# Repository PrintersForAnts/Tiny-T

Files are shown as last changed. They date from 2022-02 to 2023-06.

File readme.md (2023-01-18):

# Tiny-T (revision 2.0)



Tiny-T is a Voron Trident with build volume 150mm^3.

<p align="center">
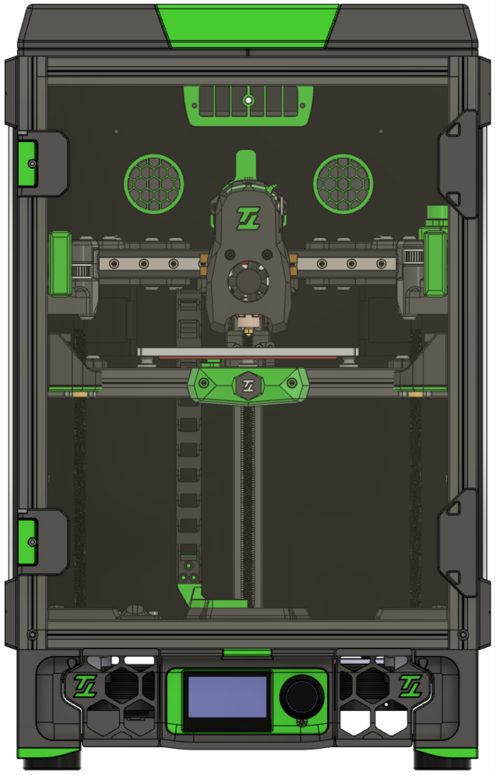
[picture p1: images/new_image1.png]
  
</p>

Source: https://github.com/VoronDesign/Voron-Trident

License: [License](./LICENSE.txt)

Changes: Tiny-T "branding" and scale modelling down.

### Changes from revision 1.0 to revision 2.0

- With the addition of the tophat, the vertical extrusions are now back to 400mm, according to Trident specifications
- Side, Front and Rear panels have reduced their height by also 25mm
- Single front door
- New door hinges and handles
- New rear panel with mounting holes for the air filter
- New bed design that support M3 screws to hold the build plate aligned

Important: if ordering panels from vendors, make sure they are using the latest DXF files

## Frame Specs

If ordering from Misumi, these are the specs:

```
Misumi HFSB5-2020-400-LCP-RCP-AV260		4 (corner extrusion)
Misumi HFSB5-2020-270-TPW 			9 (top, bottom, front[top/bottom], rear top extrusions)
Misumi HFSB5-2020-270-AH135-TPW 		1 (rear bottom extrusion)
Misumi HFSB5-2020-230-LTP			1 (rear Z extrusion)
Misumi HFSB5-2020-230				1 (x gantry extrusion)
Misumi HFSB5-2020-140				1 (rear gantry extrusion)
Misumi HFSB5-2020-270-AH135			1 (bed extrusion)
Misumi HFSB5-2020-132-LTP			1 (bed extrusion)
```

## Components

- 2x 1200mm (120cm) GATE belts
- 6x Linear Rail MGN9H 200mm - [Ali Express](https://www.aliexpress.com/item/32773296501.html?spm=a2g0s.9042311.0.0.6ea64c4dDtOd7b)
- 150mmx150mm bed - [Mandala Roseworks](https://www.mandalaroseworks.com/shop/tiny-t)
- 150mm PEI Flex build plate - [Ali Express](https://www.aliexpress.com/item/1005003157344482.html?spm=a2g0s.9042311.0.0.6ea64c4dDtOd7b)
- 120mmx120mm 120w 24v heating pad - [Keenovo](https://keenovo.store/collections/standard-keenovo-silicone-heaters/products/keenovo-square-silicone-heater-3d-printer-build-plate-heatbed-heating-pad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)
- LDO Orbiter Extruder kit - [Fabreeko](https://www.fabreeko.com/products/ldo-orbiter-extruder-1-75mm?_pos=1&_sid=68aa9064c&_ss=r) OR LDO Galileo Clockwork kit - [Fabreeko](https://www.fabreeko.com/products/ldo-galileo-clockwork-kit?_pos=1&_sid=3b0226477&_ss=r)
- 2x LDO NEMA 17 stepper motors - [Printed Solid](https://www.printedsolid.com/products/ldo-nema-17-motor-high-temp-180c-ldo-42sth40-2004mah)
- 3x V0.1 Z Stepper motor with 150mm lead screw - [Fabreeko](https://www.fabreeko.com/products/ldo-42sth25-1004cl200evrn-v0-1-z-motor?_pos=9&_sid=546ac732a&_ss=r)
- 3x GE5C bearings - [Deep Fried Hero](https://deepfriedhero.in/products/ge5c-spherical-bushing-plain-bearing?_pos=2&_psq=ge&_ss=e&_v=1.0), [Ali Express](https://www.aliexpress.com/item/1005001493222143.html?spm=a2g0s.9042311.0.0.6ea64c4dDtOd7b)
- FYSETC V2.1 RGB Mini 12864 - [Amazon](https://www.amazon.com/gp/product/B08R9ZH7S2/ref=ppx_yo_dt_b_search_asin_title?ie=UTF8&psc=1)
- Amplifier Cabinet - [Amazon](https://www.amazon.com/gp/product/B00JJ191Z6/ref=ppx_yo_dt_b_search_asin_title?ie=UTF8&psc=1), [Ali Express](https://www.aliexpress.com/item/1005001469045379.html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)

### Mods used

- [Boop](https://github.com/VoronDesign/VoronUsers/tree/master/printer_mods/Ellis/Single_MGN9H_Carriage) by `Yeri`
- [RSCS](https://github.com/VoronDesign/VoronUsers/tree/master/printer_mods/Phalanx/Other-V2-Idlers) by `Derpimus` and `DoubleT`
- [Panel Support Clips](https://github.com/VoronDesign/VoronUsers/tree/master/printer_mods/wile-e1/Deck_Panel_Support_Clips) by `wile-e`
- [Tophat](https://github.com/jakub874/Jakub3DPrinterMods/tree/main/Tophat) by `jakub874`

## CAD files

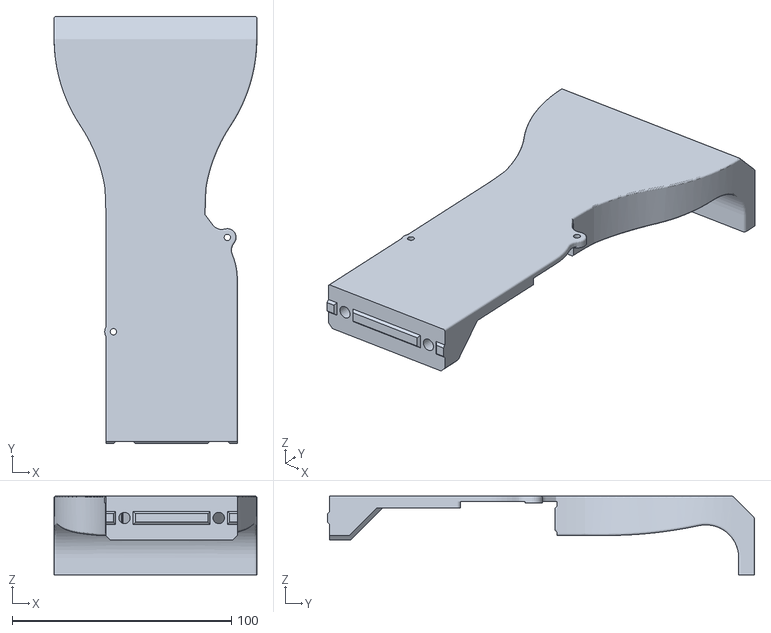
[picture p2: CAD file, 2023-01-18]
MODS/rscs/STLs/main_body_x2.stl
92.5 x 194.7 x 36.0

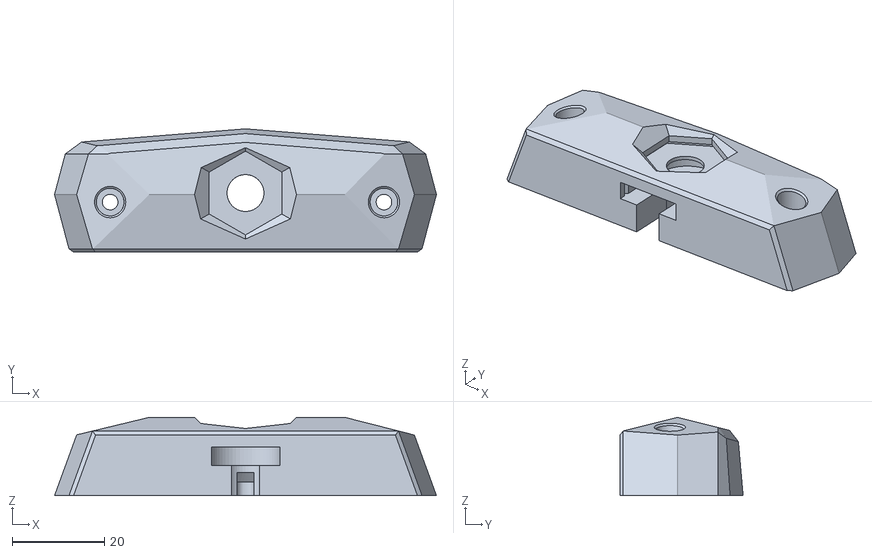
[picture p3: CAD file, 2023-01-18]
STLs/extras/stealth_bed/[a]_main_body.stl
82.8 x 26.7 x 17.0

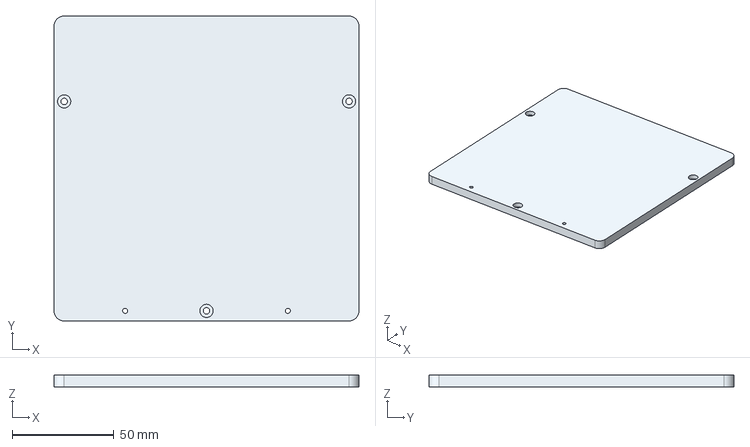
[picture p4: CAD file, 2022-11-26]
CAD/150mm_MIC6.step
150.0 x 150.0 x 6.00 mm

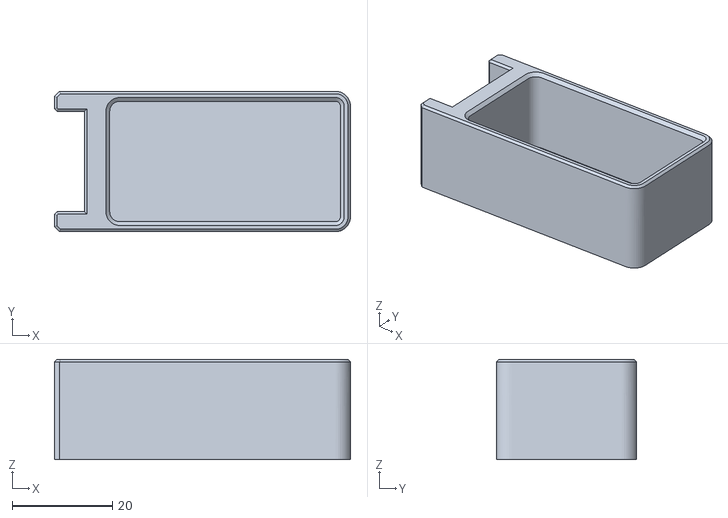
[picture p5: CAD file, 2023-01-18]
MODS/nozzle_wiper/nozzle_wiper_basket.stl
59.0 x 28.0 x 20.0

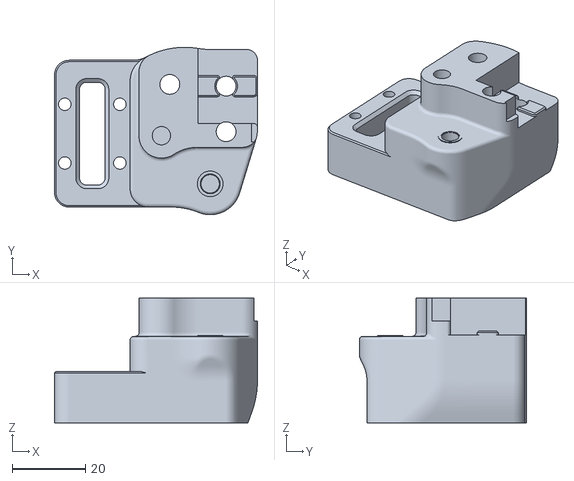
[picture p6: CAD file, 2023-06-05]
MODS/pin_mod/xy_left_bottom.stl
55.3 x 45.6 x 34.0

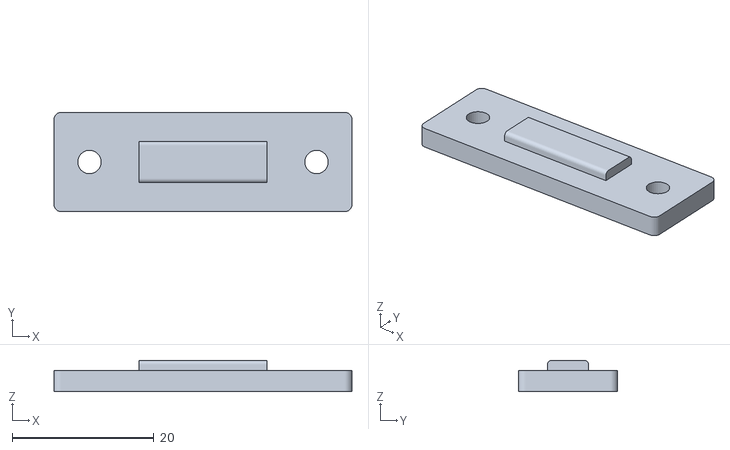
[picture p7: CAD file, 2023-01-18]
MODS/rscs/STLs/fans_pcb_spacer.stl
42.0 x 14.0 x 4.40

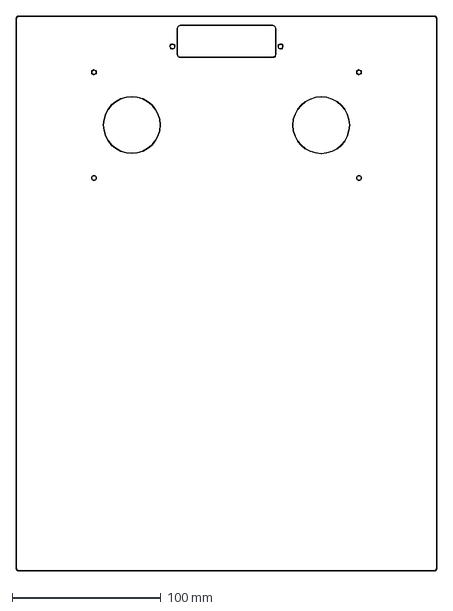
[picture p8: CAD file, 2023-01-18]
panels/acm/Tiny-T_Rear_Panel_air_filter.dxf
283.0 x 373.0 mm

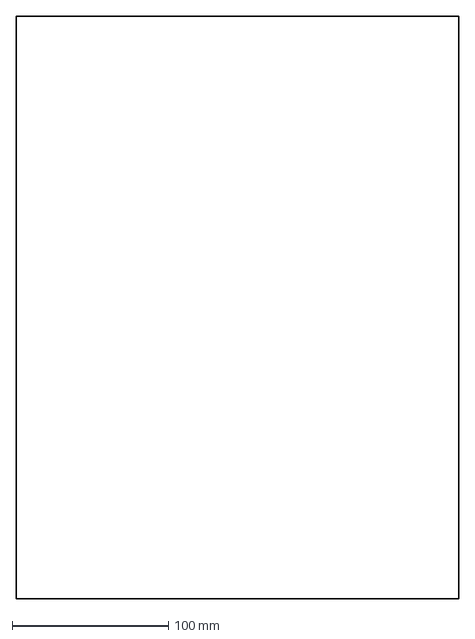
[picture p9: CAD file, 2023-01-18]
panels/acrylic/Tiny-T_Side_Panels_x2.dxf
283.0 x 373.0 mm

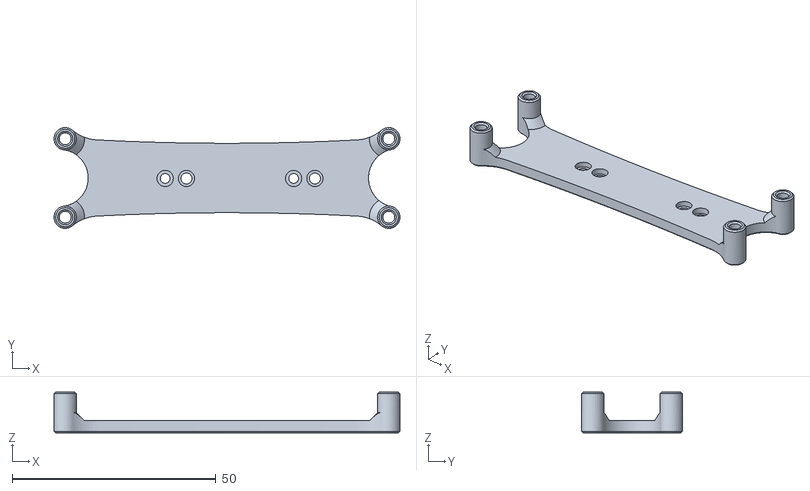
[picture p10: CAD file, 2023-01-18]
STLs/electronics/controller_mounts/u2c_universal_mount.stl
84.8 x 24.7 x 10.0

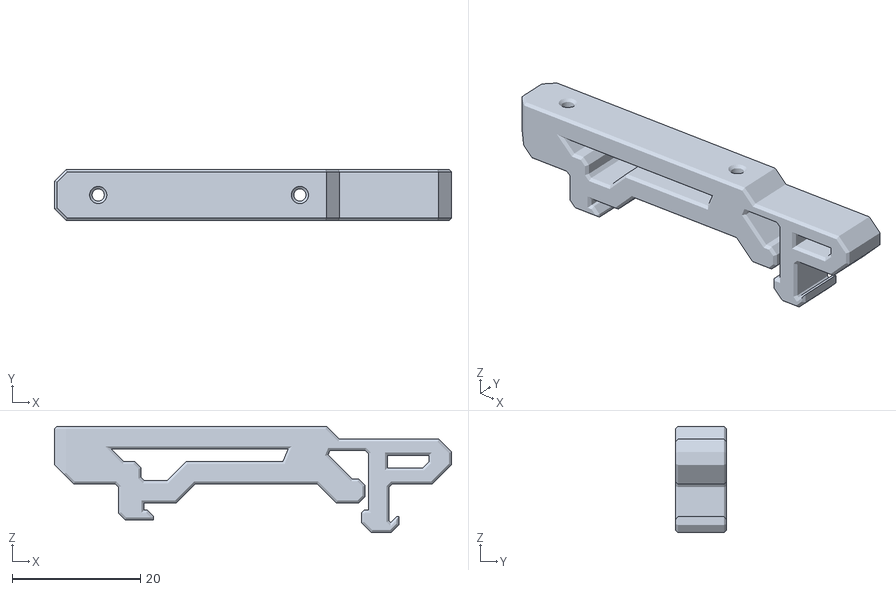
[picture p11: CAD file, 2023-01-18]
STLs/electronics/pcb_din_clip.stl
62.0 x 8.00 x 16.6

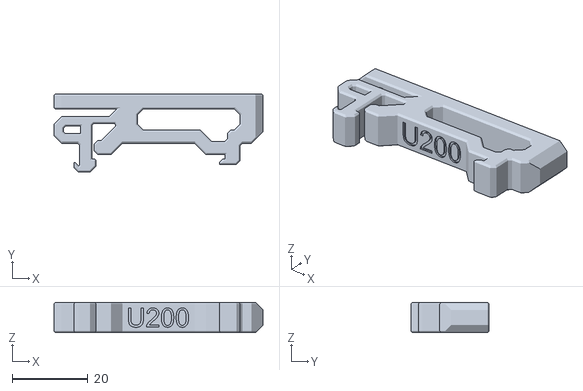
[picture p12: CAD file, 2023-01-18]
STLs/electronics/psu_mounts/UHP_200_Mount_x2.stl
55.0 x 20.6 x 8.00

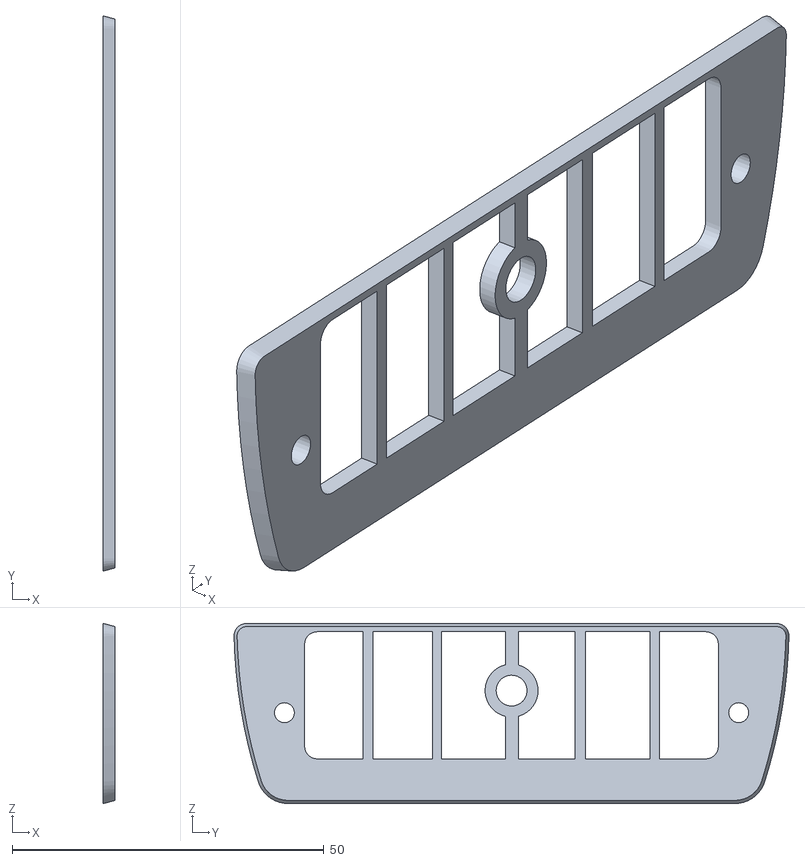
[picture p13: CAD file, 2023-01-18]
STLs/extras/air_filter/nevergrater_inside_cover.stl
2.00 x 89.0 x 28.9

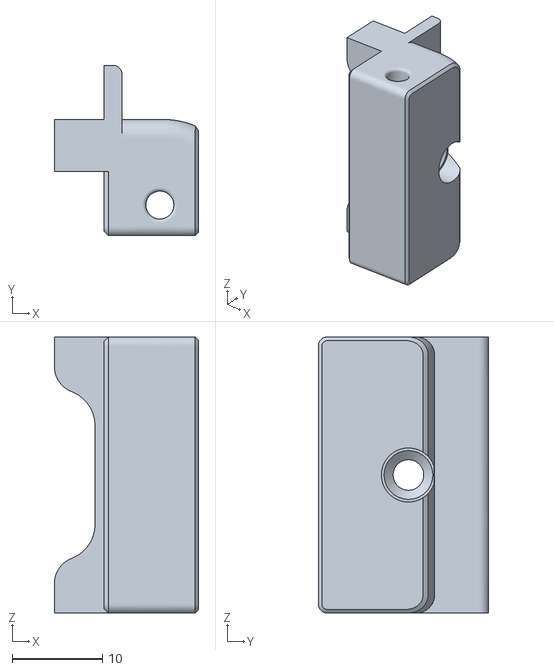
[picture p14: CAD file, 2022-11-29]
STLs/extras/door_hinges/[a]_hinge_pivot_x2.stl
16.0 x 18.9 x 30.6

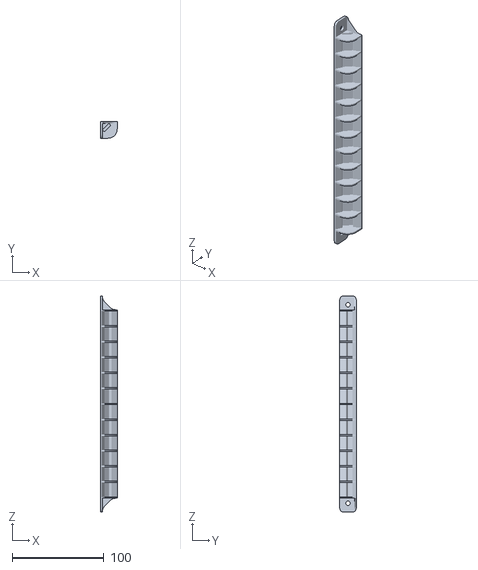
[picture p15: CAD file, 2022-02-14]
STLs/extras/lightbar/lightbar-right.stl
18.0 x 18.0 x 235.6

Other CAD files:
STLs/extras/other_idlers/front_idler_bottom_x2.stl
STLs/extras/panel_clips/2020_panel_clips_x8.stl
STLs/extras/stealth_bed/led_carrier.stl
STLs/extras/umbilical/[a]_wire_cover.stl
CAD/160mm_MIC6.step
MODS/nozzle_wiper/nozzle_wiper.stl
MODS/pin_mod/a_bottom.stl
MODS/pin_mod/a_top.stl
MODS/pin_mod/b_bottom.stl
MODS/pin_mod/b_top.stl
MODS/pin_mod/xy_left_top.stl
MODS/pin_mod/xy_right_bottom.stl
MODS/pin_mod/xy_right_top.stl
MODS/rscs/STLs/spacer_x4.stl
STLs/Z_assembly/Z_endstop_pcb_mount_bottom.stl
STLs/Z_assembly/Z_endstop_pcb_mount_top.stl
STLs/Z_assembly/Z_endstop_pcb_mount_top_mirror.stl
STLs/Z_assembly/drag_chain_bottom.stl
STLs/Z_assembly/drag_chain_top.stl
STLs/Z_assembly/wago_221-412_mount.stl
STLs/Z_assembly/z_stepper_motor_mount_left.stl
STLs/Z_assembly/z_stepper_motor_mount_rear.stl
STLs/Z_assembly/z_stepper_motor_mount_right.stl
STLs/Z_assembly/z_wires_cover.stl
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

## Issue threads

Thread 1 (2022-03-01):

Z Motors

spotless20, 2022-03-01:
Hey, at first my full respect and thx to upsetting this guide :)

You write 3x 150mm V0.1 Motors, this are 200mm you linked and build in the v0.1.

Im just dump and misunderstood smth or is this okay so?

And 2nd. I can use the printer with the normal Steahlth/Afterburner and the Mini?

Thx and best Wishes.

Closed 2022-03-01.

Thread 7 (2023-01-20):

Toolheads missing

W141-ID, 2023-01-20:
Either I am unable to find the toolheads or they are missing, wanted to print the mini stealthburner with the tiny-t logo

thiagolocatelli, 2023-02-28:
[miniSB_DoubleT.step.zip](https://github.com/PrintersForAnts/Tiny-T/files/10855562/miniSB_DoubleT.step.zip)
@W141-ID in case you still needed

Closed 2023-02-28.

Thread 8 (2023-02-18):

BOM

kobzzon, 2023-02-18:
Do you have a BOM list of bolts and nuts?

thiagolocatelli, 2023-02-28:
@kobzzon its basically the Trident BOM

kobzzon, 2023-03-10:
thanks

Closed 2023-03-10.

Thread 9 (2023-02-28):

Front idlers not in step file

flow23, 2023-02-28:
Hi,
the front idlers from the github image is not in the step file.

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

thiagolocatelli, 2023-02-28:
@flow23 I shared the step file for those idlers in one of the TinyT build logs in the Doom Discord server. check it out.

thiagolocatelli, 2023-02-28:
[front idlers v5.step.zip](https://github.com/PrintersForAnts/Tiny-T/files/10855531/front.idlers.v5.step.zip)
 @flow23 here they are in case you cant find.

flow23, 2023-03-01:
Hi Thiago, is there a reason why you don't include it?

Closed 2023-02-28.

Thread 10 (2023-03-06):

MiniSB Cowling

two-cees, 2023-03-06:
Is the Tiny-T branded mini SB cowling somewhere else? I don't see it in the STLs or CAD for this revision.

thiagolocatelli, 2023-03-06:
Take a look at issue #7, I uploaded the step file there. @two-cees

Closed 2023-03-06.

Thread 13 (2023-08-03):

wrong RSCS link

Laroto, 2023-08-03:
The link leads to "other idlers".
Also, what fans does the RSCS use?

thiagolocatelli, 2025-01-13:
if I am not mistaken, I have added the RSCS into the CAD.

Closed 2025-01-13.

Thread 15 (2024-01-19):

Example configuration missing

Laroto, 2024-01-19:
There is no configuration example in the files.

The gap between a new Voron builder and a TinyT builder is quite large due to the unofficial dimensions.
Could someone add a example file?

thiagolocatelli, 2024-01-19:
@Laroto Pedro, aqui tem um exemplo de config: https://github.com/DoubleT-PrinterConfigs/TinyTConfig

thiagolocatelli, 2024-01-19:
also config added to readme.md file through pull request

Closed 2024-01-19.

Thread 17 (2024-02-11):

Direct access to Tiny-T_r2_Master.step.zip instead of zip file

izanamisu, 2024-02-11:
Hi,

We are using an addon for fusion360 called Voron-Construct ( https://github.com/PrintersForAnts/Voron-Construct)
The addon gives us acces to step files to use in fusion.

The printer files are ziped and are not available in the addon, can you guys unzip and upload the step files to the cad repositories?

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

thiagolocatelli, 2025-01-13:
```
remote: Resolving deltas: 100% (2/2), completed with 2 local objects.
remote: error: Trace: 3b6a80520f795821b249ebf358b16cc7f44b9a312a17ee540662215fd383eaf4
remote: error: See https://gh.io/lfs for more information.
remote: error: File CAD/Tiny-T_r2_Master.step is 157.85 MB; this exceeds GitHub's file size limit of 100.00 MB
remote: error: GH001: Large files detected. You may want to try Git Large File Storage - https://git-lfs.github.com.
```

Closed 2025-01-13.

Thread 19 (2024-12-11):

Magnetic bed CAD file

staticvoid255, 2024-12-11:
Hi there,

Wondering if there's a CAD file for the magnetic version of the bed sold by Mandala, as I would like to machine the place myself

Cheers!

thiagolocatelli, 2024-12-11:
Thats something only the Mandala vendor has.

Closed 2024-12-11.

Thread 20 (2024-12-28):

Doors frame-side magnet holders have uneven recess lengths (5.3 + 4.8mm instead of 6mm both)

fff7d1bc, 2024-12-28:
The printed part that gets into the frame and holds magnets have two recessed standoffs, both of which have different length.

Using the included step file and upper magnet holder the first have 5.3mm from the top of extrusion to the end of recess and the other standoff on the same printed part have just 4.8mm.

I noticed in my build that if I tighten the bolt holding those the magnet holder tilts and make things not fit well. To solve this i checked my Misumi 2020s and they are 6mm deep so I decided to just use extrude tool and extend those to be 6mm and while doing so I noticed that they are not only too short for BOM Misumi frame, they are also uneven length on both ends!

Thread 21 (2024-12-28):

Skirt 60mm fan mount have less than 60mm in CAD for the fan

fff7d1bc, 2024-12-28:
The fan mount meant for 60mm fan seems to be about 59mm in the CAD, when you add into it the printing tolerances it might be very difficult fit for the fan there.

I was doing some remix of it since I need the fans to not extend into the chamber, therefore I went with 60x15 fans instead and was adjusting it to better fit my fans, initially I though my fans are out of spec but they actually are 60.02mm and the printed part out of ASA GF came at 59.2mm for the fan space.

thiagolocatelli, 2025-01-13:
I noticed that. New STL added

Closed 2025-01-13.

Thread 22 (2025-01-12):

Panels: missing DXF for bottom electronics cover

fff7d1bc, 2025-01-12:
It seems that there's no DXF for the bottom-most panel that is supposed to cover electronics. There isn't one in CAD either but the skirts do have place for heatsets suggesting there might be a plan for panel there

thiagolocatelli, 2025-01-13:
yeah, being such a tiny printer I never bothered creating a a DXF file for the bottom. If you want one, I can create and upload.

thiagolocatelli, 2025-01-13:
actually looking at the CAD now, only the rear skirts have holes for the panel. I will fix it by adding holes to the remaining skirts and adding the panel to the CAD and the DXF file to the folder too

thiagolocatelli, 2025-01-13:
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

fff7d1bc, 2025-01-13:
Thanks, I intentionally did not ordered it when I was getitng my panels CNC'd and now that I was working on another order I figured I might, but I do not feel the need for it so no need for you to go out of your way to add it if you also intentionally left them out in first place

Closed 2025-01-13.

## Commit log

2022-02-14 Moving to PrinterForAnts
    [150mm_MIC6_1.stp, MGN12H_Carriage_Left.stl, MGN12H_Carriage_Right.stl.stl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]
2022-11-15 Added AB drives for nema14
    [a_drive_frame_lower_nema14.stl, a_drive_frame_upper_nema14.stl, b_drive_frame_lower_nem14.stl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]
2022-11-26 Added tophat and cad for AB nema 14
    [MagTopPanel-Base_150_x4.stl, MagTopPanel-Edge_150_x4.stl]
2022-11-26 Updated 150mm bed and add 160mm bed step files
    [150mm_MIC6.step, 150mm_MIC6_1.stp, 160mm_MIC6.step]
2022-11-26 updated cad with new mods and features
2022-11-29 Updated rear panel and front door, added mounting holes to air filter housing
    [Tiny-T_Front_Door.dxf, Tiny-T_Front_Doors.dxf, Tiny-T_Side_Panels.dxf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]
2022-11-29 Added door hinges
    [[a]_hinge_pivot_x2.stl, [a]_hinge_pivot_x4.stl, door_handle_a_x2.stl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]
2023-01-18 Revision 2
    [2020_panel_clips_x8.stl, Pt1.stl, Pt2.stl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]
2023-01-18 Removed old files
    [boop_center_left.stl, boop_center_right.stl, boop_center_switch.stl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]
2023-05-14 Removed old idlers
    [[a]_front_idler_cover_x2.stl, [a]_front_idler_inlet_x2.stl, [a]_tensioner_left.stl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]
2023-05-14 renamed folder
    [[a]_front_idler_cover_x2.stl, [a]_front_idler_inlet_x2.stl, front_idler_housing_cover_x2.stl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]
2023-06-04 Added pin mod
    [a_bottom.stl, a_top.stl, b_bottom.stl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]
2023-11-08 added holes for bottom panel matching rear skirts
    [front_skirt_a_150_tiny-t.stl, front_skirt_b_150_tiny-t.stl]
2023-11-08 New version added with added hole and no extra space in filename
    [front_skirt_b_150 _tiny-t.stl]
